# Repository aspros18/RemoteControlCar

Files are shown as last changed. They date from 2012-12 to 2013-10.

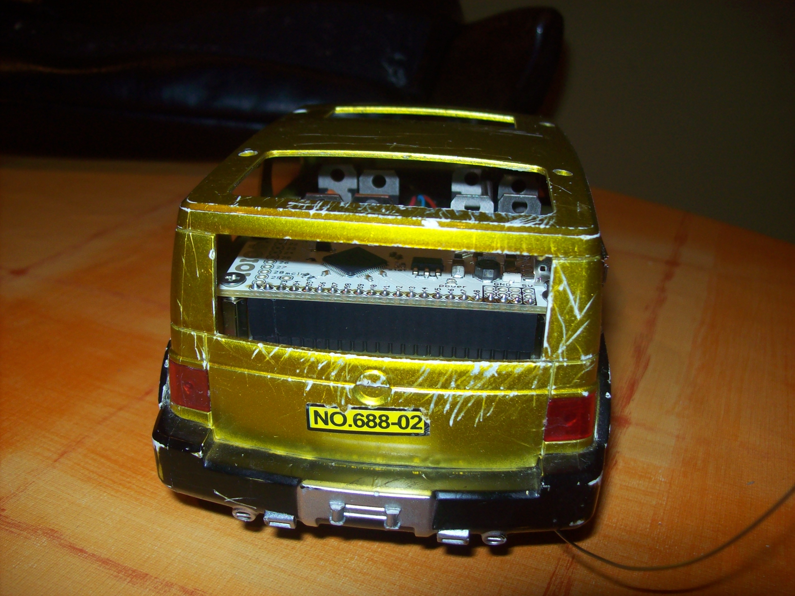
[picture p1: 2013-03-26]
photos/testmodel_bottom.JPG

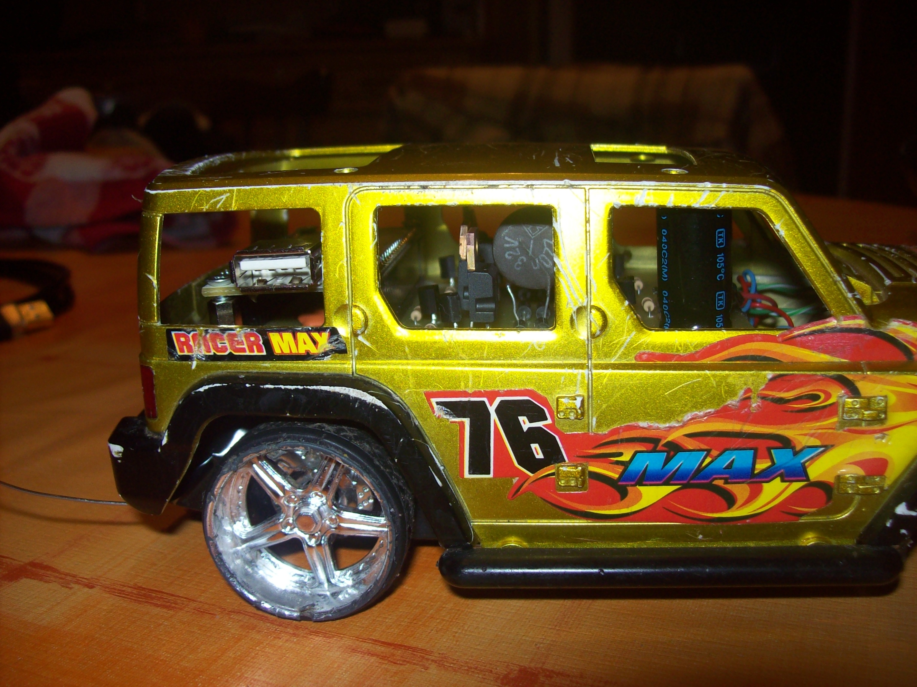
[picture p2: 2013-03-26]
photos/testmodel_side.JPG

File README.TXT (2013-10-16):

Git URL: https://github.com/fzoli/RemoteControlCar

Beszerzés
---------

Hordozható kiadás:
https://github.com/fzoli/RemoteControlCar/raw/master/bin/rel-portable.zip

Windows telepítő:
https://github.com/fzoli/RemoteControlCar/raw/master/Setup.msi

Linux telepítő:
https://github.com/fzoli/RemoteControlCar/raw/master/linux-installer.bsx

OS X telepítő:
https://github.com/fzoli/RemoteControlCar/raw/master/mac-installer.dmg

Android alkalmazás:
https://github.com/fzoli/RemoteControlCar/raw/master/android/RemoteControlCar/bin/RemoteControlCar.apk

A projektet bemutató videófelvételek a videos könyvtárban találhatók meg.
A járműről fényképek a photos könyvtárban, képernyőképek a snapshots
könyvtárban. A szakdolgozat digitális változata: thesis.pdf

Bevezetés
---------

A projekt célja egy távirányítós autó vezérlése interneten át.

Az autó vezérlése Android operációs rendszerrel futó mobiltelefon segítségével valósul meg.

A telefon felhasznált eszközkészlete:
- hátsó kamera, ami segítségével lehet látni, mi van az autó előtt
- giroszkóp, ami segítségével meg lehet tudni a gyorsulás és kanyarodás mértékét valamint az út lejtését (ha nincs fék az autón, az emelkedő/lejtő adat alapján megoldható, hogy egy helyben álljon az autó bármikor, ha azt akarjuk)
- GPS vevőt, ami segítségével megbecsülhető a pillanatnyi sebesség és megtudható a kellően pontos tartózkodási hely
- USB port, ami segítségével - egy SparkFun által gyártott mikrovezérlő - az IOIO for Android (DEV-10748) köthető össze a telefonnal. A mikrovezérlőhöz tartozik egy Java nyelvre írt API, ami segítségével ADB (Android Debug Bridge) vagy ADK (Accessory Development Kit) kapcsolaton keresztül a telefon képes kommunikálni a külvilággal. Az API automatikusan kapcsolódik az eszközhöz, nem fontos, melyik kapcsolaton keresztül, de az ADB van előnyben részesítve.
- mobilhálózat, ami segítségével HSPA vagy 3G mobilinternetet használva elküldhető a videó jel, a statisztika és foghatóak a vezérlő jelek
- mobilakku, ami ellátja a mobiltelefont árammal. Azt is jó látni interneten keresztül, hány %-on áll az aksi.

A mikrovezérlő célja:
- vezérelni az autót a telefonnal
- az autó akkumulátorának töltöttségi szintjének megszerzése

Egyéb eszközök:
- kézzel állítható, kétállású kapcsoló, ami eldönti, hogy a beépített mikrovezérlő (ami a gyári távirányító jelének segítségével vezérli az autót) vagy a telefon mikrovezérlője (ami az internetről kapott utasításokkal vezérli az autót) legyen aktív. Erre azért van szükség, hogy ne történhessen meg az, hogy mindkét mikrovezérlő egyazon időben jelzést adjon le és túlfeszültséget okozzon az autó áramkörében
- a lista még bővülni fog olyan dolgokkal mint pl. ellenállás

A hálózati kommunikáció terve:
------------------------------

A kommunikáció SSL titkosítást használva socketek segítségével történik.
A tanúsítványokban szereplő CN (Common Name) mező alapján történik a felhasználó számítógépek és emberek azonosítása, tehát nincsenek felhasználónevek és jelszavak.
Az összes tanúsítvány egyetlen kiállítótól (CA) származik és mind a socket szerver, mind a socket kliensek csakis ebben az egy kiállítóban bízik meg.
Ez azt eredményezi, hogy az összes olyan tanúsítványt elfogadják, amiket a konkrét CA állított ki, de az összes többit elutasítják.

Az SSL többféle próbának is aláveti a socketeket mielőtt létrejönne a kapcsolat:
- megnézi, hogy megbízható-e a tanúsítvány (vagyis inkább a CA)
- megnézi, hogy nem járt-e le a tanúsítvány
- ellenőrzi a hostnevet

A hostnév-ellenőrzés ki van kapcsolva, mert a szabvány szerint a szerver hostnevének és a tanúsítványában szereplő CA mezőnek meg kell egyeznie.
Fentebb írtam, hogy a CA mezőt én a felhasználók azonosítására használom (amolyan felhasználónév szerűség), másrészt a szervernek nem feltétlenül van hostneve vagy a hostnév változó (Pl. IP cím alapján is lehet szerverhez kapcsolódni).

Az egyszerűsített kapcsolati ábra:
Host <-> Bridge <*> Controller

Jelmagyarázat:
<-> egy-egy kapcsolat
<*> egy-sok kapcsolat
Host: a mobiltelefon által indított kliens socket (magyarban is host)
Bridge: egy olyan socket szerver, ami kliens socketek kapcsolódására vár (magyarra fordítva: híd)
Controller: azok a kliens programok, amik segítségével vezérelhető az autó (magyarra fordítva: vezérlő)

Host:
-----

Socket oldalról megközelítve:
A host az én esetemben egy mobiltelefon, ami legtöbbször mobilinternetet - ritkábban Wi-Fi hálózatot és akkor belső IP alapján is lehet címezni - használ  arra, hogy fel tudja venni a kapcsolatot a híddal. Socket szempontjából ő kliens szerepet tölt be. Ennek az az oka, hogy az összes internetes IPv4 cím ki lett már osztva és az internetszolgáltatók minden trükköt bevetnek, hogy ki tudják szolgálni az összes internetet használni akaró gépet. A mobilszolgáltatók ezért NAT-olt IP címet osztanak ki a mobilinternetet használó gépeknek. Ezzel a trükkel egy internetes IP cím (rövidebben WAN IP) több géphez is tartozhat, tehát több gépet ki lehet szolgálni, de van egy hátránya is - amiről a mobilinternetezők nagy része nem is tud - mégpedig az, hogy nincs egy elérhető aktív port sem. Mivel nincs aktív port, hiába üzemeltetünk szervert a telefonon, azt az internetről nem lehet elérni, vagyis csak kliens szerep lehetséges.

A kamera elérése:
A telefon kamerájának képkockái MJPEG streameléssel jutnak el a hídhoz.
Eredeti elképzelésem szerint saját magam olvastam volna a kamera képét és küldtem volna a socket servernek.
A probléma ott kezdődött, hogy az android API nem éppen programozóbarát ha médiáról van szó.
Egyrészt csak akkor hajlandó képkockákat adni, ha azt felületen is megjelenítem (és ennek nem sok értelme van) valamint az eseménykezelőben egy bájt tömböt kapok, amiben YUV formátumú kép van. Ezzel még nem is lenne gond, mert ha valakinek csak a fekete-fehér tartomány kell, akkor még örül is neki, de ha színes képet szeretne az én telefonom kb. 800 ezredmásodpercig dolgozik rajta és akkor még nem is méreteztem át, nem is tömörítettem JPEG formátumba. Olyan 0.7 FPS érhető el így összességében. Gondoltam utánanézek már kész androidos programoknak, amik tudnak videót streamelni. A sok androidos program közül egy megfelelően működőt találtam is, aminek a neve IP Webcam. Java csomag alapján keresve "com.pas.webcam". Ez volt az egyetlen olyan program, ami már megfelelő FPS-t tudott és nem észleltem késést sem. Meg is néztem az okát (hogy hogyan, az már más kérdés). Natív kódot használtak fel, amit C nyelven írtak meg. (Az Android is támogatja a natív kódokat. Bővebben: NDK - Native Development Kit)
Az IP Webcam program HTTP szervert használ és lehetőség van felhasználónév és jelszó beállítására, valamint megadhatjuk a szerver portját, a JPEG képek paramétereit (felbontás, FPS, képminőség) és hogy induljon-e el a telefon indulásakor a program, hogy bármikor hozzá lehessen férni a kamerához.

A telefonon futó program terve:
A telefonon egy Android service fog futni, amit egy egyszerű Activity felületről lehet majd elindítani ill. leállítani.
A service ha leállítódik valami ok miatt (pl. kevés a memória), úgy lesz beállítva, hogy amint lehetséges, induljon el.
Ha a telefon újraindulna miközben a service fut (pl. SD kártyáról fut vagy 100 program és szegény kártya nem bírja olyan gyorsan adni az adatokat mint kéne), a service az OS (operációs rendszer rövidítése) felállása után szintén elindul.
A service az elindulása után azonnal kapcsolódni próbál a hídhoz, ha nem sikerül percenként próbálkozik.
Ha a kapcsolat megszakad, azonnal elindul a kapcsolódás folyamata.
Ezzel minden nem várt hibára megtörtént az óvintézkedés.
A service elindulásakor, ha nem fut az IP Webcam program, akkor az API-ja segítségével a service elindítja azt. (Az ip-webcam könyvtárban további infó.)
A service elindítása előtt a felületen a menüből kezdeményezhető további beállítás.
Itt kell megadni:
- a híd címét (host vagy IP) és portját (amin a socket servlet figyel)
- a tanúsítvány publikus kulcsát (crt fájl) és privát kulcsát (key fájl), amivel a hídhoz kapcsolódik és titkosít.
- a tanúsítvány kiállítójának publikus kulcsát
- mennyi időközönként küldjön statisztikát a telefon
Opcionális beállításként megadható a híd tanúsítványának CN mezője, csak a biztonság kedvéért.
Előfordulhat, hogy rossz címet állítottunk be és nem a híd van címezve. Ez esetben ha a CN mező meg van adva, kiküszöbölhető a fölösleges kapcsolódás és azonnal egyértelmű hibajelzést kapunk. Ha nincs megadva a CN mező, a program percenként fölöslegesen fog próbálkozni, konkrét hibát nem jelezve.

A hang stream, eredetileg kikapcsolt és kérhető lesz bekapcsolásra. Kikapcsolása esetén elég a socket streamet lezárni és kezelni kell a kivételt.
A streamet az android beépített szolgáltatása (MediaRecorder.AudioEncoder.AAC) fogja szolgáltatni és a híd fogja tovább adni a vezérlőknek.

Bridge:
-------

A hídnak két szerepköre van:
- vár a hostra - amitől a videót és a statisztikát kapja és akinek a vezérlőjelet küldi majd
- kiszolgálja a vezérlőket - amik irányítani szeretnék az autót - és eldönti, hogy ki vezérelheti az autót, ha több kérés van egy időben

Úgy terveztem meg a socket alapú kommunikációkat, hogy a híd el tudja dönteni, mi célja lesz a kapcsolatnak és egy időben több kapcsolatot kezelhessen.
A híd esetén a host CN mezőjét kötelező megadni, mert a híd ez alapján tudja, hogy a socket kliens vezérlő-e vagy host. EZ NAGYON FONTOS!!!
A híd esetében megadható több CN mező is, amik segítségével lehet tudni, mely tanúsítványok lesznek a hostok ha esetleg több autó is távvezérelt lesz a jövőben. (Meg lehetett volna oldani úgy is, hogy a socket kliensek még a kapcsolatazonosító kérése előtt közölték volna, hogy ők hostok vagy vezérlők, de ez esetben a híd nem tudna pontos listát adni a hostokról.)

[Opcionális terv: A híd mellé lehetne egy webszervert is tenni. Regisztrálhatnának internetről mások, akiknek el lett adva egy ilyen autó és van hozzá mobiltelefonjuk. A webszerver is SSL-t használna az alapértelmezett 443-as porttal. Itt akár tanúsítványt is generáltathatnának (hostjukhoz és vezérlőjeikhez) így a híd socket servere megbízhatónak találná őket és szintén tudná ki a host és ki a vezérlő. A híd szolgáltatása havidíjas is lehetne és azoknak lenne jó, akik nem szeretnének saját híd szervert üzemeltetni. A host mikrovezérlő kódját ez esetben úgy kellene megtervezni, hogy interface alapú legyen és a felületről több autó típust lehessen választani az implementált osztályok alapján. Szép álom lenne, ha a mobilinternetes szolgáltatókkal meg lehetne egyezni, hogy ne mérjék a forgalmat és kapnak a bevételből :-) ]

Host felőli kapcsolatok:
1. MJPEG stream: hídnak letöltés, hostnak feltöltés
2. Statisztika adatok: objektumos stream, hídnak letöltés, hostnak feltöltés
3. Vezérlő parancsok a hídtól (az autónak és a telefonon futó programnak): objektumos stream, hídnak feltöltés, hostnak letöltés

Vezérlő felőli kapcsolatok:
1. MJPEG stream: hídnak feltöltés, vezérlőnek letöltés
2. Statisztika adatok (a hostról és a hídról): objektumos stream, hídnak feltöltés, vezérlőnek letöltés
3. Vezérlő parancsok a vezérlőtől (a hostnak és a hídnak): objektumos stream, hídnak letöltés, vezérlőnek feltöltés

Bővebb magyarázat:
- A kapcsolatok előtt a számozás kapcsolatazonosítót és prioritási sorrendet is jelent.
- A híd a hostnak főként autóvezérlő utasításokat közöl (a 3-mas kapcsolaton át), de a telefonnak közölheti azt is,
  hogy hagyja abba az MJPEG streamelést vagy éppen kezdje el.
- A vezérlő a hídnak főként autóvezérlő utasításokat ad, de üzenhet a hídnak is, hogy szeretné átvenni az autó irányítását.
- A híd is üzenhet a vezérlőnek, ha éppen elvették tőle az irányítást, jelezze a felületen.

A kapcsolat kialakítása a következő módon valósul meg:
A kliens három kapcsolatot alakít ki ugyan azzal a sockettel, a kapcsolat létrejötte után új szálban kezdődik meg a feldolgozás.
A szerver amíg aktívan fut (tehát a Socket server nincs bezárva) cikluson belül mindig várja a klienseket és ha létrejön egy SSLSocket, ő is külön szálban dolgozik vele tovább, hogy képes legyen több kapcsolatot kiszolgálni egy időben.

A kapcsolat kialakításának lépései: (Szerver alatt a híd socket szerverét értem.)
0. A kliens socket kapcsolódik a szerver sockethez és sikerül az SSL kézfogás, létrejön a kapcsolat és mindkét oldalon egy SSLSocket objektum.
1. a) A szerver a kliens-tanúsítvány CN mezejének alapján megtudja, hogy a kliens host vagy vezérlő és hogy pontosan kivel is van dolga.
   b) A szerver megnézi, hogy az adott szerepkörben az adott névhez hány kapcsolat van már kialakítva.
   c) A szerver inkrementálja a B pontban kapott számot és így megkapja az aktuális kapcsolat azonosítóját
      és a fenti felsorolás alapján már tudja is, mire lesz használva a kapcsolat.
2. A szerver elküldi a kliensnek a kapcsolatazonosítót. Másképp fogalmazva: A kliens lekéri a kapcsolatazonosítót.
3. Mindkét oldal a kapcsolatazonosító alapján együttműködve kezeli a kapcsolatot.
4. Bármelyik oldal lezárhatja a kapcsolatot, ha úgy dönt. Ekkor befejeződik a kommunikáció.

Ha a hídra ugyan azzal a tanúsítvánnyal kapcsolódnak több helyről, a híd a régebbi kapcsolatokat bezárja.
Így ki van kerülve az, hogy két helyről vezérelhessék az autót ellentmondásos üzenetet leadva mint pl. menj jobbra és balra is.

Jogkezelés:
Előfordulhat olyan eset, hogy egy autót több vezérlő is szeretne irányítani.
Erre azt találtam ki, hogy csinálok a hídra egy tanúsítvány-prioritás listát.
A nagyobb prioritású vezérlő bármikor elveheti a vezérlést a kisebb prioritású vezérlőktől, de egyébként minden vezérlő kapcsolódhat a hídhoz és minden
információt láthat, csak a vezérléstől vannak megfosztva.
Amint felszabadul a vezérlés, bárki kérheti az autó vezérlését prioritástól függetlenül és meg is kapja.
(Kérni lehet akkor is, ha éppen vezérlik az autót, de az csak kérvényt jelent, semmi többet. Amint felszabadul a vezérlés az első kérvényt benyújtó meg is kapja.)
(Ha a prioritáslistában egyetlen név szerepel, akkor úgy fog funkcionálni, mint ha root lenne, mivel mindenki felett áll ez esetben.)
Ha nagyobb prioritású kapcsolódik a hídhoz, mint aki vezérli az autót, addig amíg nem kéri a vezérlést, nem veszi el a híd az aktuális vezérlőtől az irányítást.
Aki nem szerepel a prioritáslistában, az olyan, mint ha a legutolsó utolsó helyen szerepelne a listában és a többi - listában nem szereplő - felhasználóval egyenrangúnak számít, tehát ők egymástól nem tudják elvenni a vezérlést.
Ha a vezérlő sokáig nem cselekszik, tehát nincs a gép előtt, a vezérlést elveszi a híd tőle.

Internet sávszélesség:
A híd létrejöttének fő célja az volt, hogy egyetlen egy kapcsolat (ami valójában három socket kapcsolat) legyen a mobilinternet oldaláról és az is takarékos legyen mivel forgalom- és sebességkorlátos az internet.
A hídba be van téve egy olyan sávszélesség csökkentő funkció is, hogy csak akkor kéri az MJPEG streamet a hosttól, ha van legalább egy vezérlő kapcsolódva hozzá.

Konfig fájl:
A híd esetén is meg kell adni a tanúsítvány publikus és titkos kulcsának az elérhetőségét és a kiállító publikus kulcsának az elérhetőségét.
A tanúsítvány prioritásokat és a hostlistát is itt kell megadni, de ha bevezetésre kerül egy webes felület, átkerülnek egy közös adatbázisba.

Controller:
-----------

A vezérlő az a program, ami megjeleníti az autó adatait és ha van lehetősége vezérli az autót.
Ez egy PC-n futó java alapú desktop alkalmazás lényegében, ami szintén a hídhoz kapcsolódik socket kliensként.
A felületen lehetőség van - és kötelező is első induláskor - beállítani a híd címét és portját valamint a tanúsítvány publikus és titkos kulcsát és a kiállító publikus kulcsát.
A kiállító kulcsára azért van szükség mert kliens oldalon is ellenőrizve van a szerver tanúsítvány megbízhatósága, nem csak szerver oldalon, hogy a man-in-middle támadás lehetetlen legyen.
A vezérlés billentyűzet és egér segítségével történik.
Az egérrel pontos utasítást lehet adni mind sebesség, mind irány terén.
A billentyűzettel egyszerűbb, de durvább irányítást érhet el a felhasználó és több vezérlés mód közül választhat.
(A vezérlési módok a durvaságot szabályozzák pl. előre nyílra egyenletesen gyorsuljon fel vagy földkaparással max grafttal induljon el)

Egy kis trükk:
--------------

Egyes mobilszolgáltatók csomagjaiban a webböngészés nem számít bele a forgalomkorlátba.

Ez esetben socketek helyett mondjuk Tomcat webszervert lehetne használni.
- A terv lényege ugyan az, csak a kapcsolatazonosítók helyett HTTP címzés lenne használva.
- Az MJPEG stream HTTP POST-tal streamelhető a hídnak - ami a Tomcat webszerver.
- A vezérlő utasítások JSON-nal objektummá alakíthatók Stringből és objektumból Stringre, és a HTTP tartalom is gond nélkül használható streamelés céljára.

UPDATE: Utólag kiderült, hogy csak a letöltés nem számít bele, és mivel a telefonon a kliens 99%-ban feltöltést bonyolít le, elvetett ötlet.

Továbbfejlesztés
----------------

További két socket kapcsolat segítségével megoldható lenne, hogy a telefon mikrofonjából megkapjuk a hangot is a kép mellé és a vezérlő számítógép mikrofonjából meg a telefonon játsszunk le hangot.
A telefonból érkező hang stream ki/be kapcsolható lenne, alapértelmezetten ki lenne kapcsolva takarékosság miatt.
Az autót vezérlő kliens tudná csak ki/be kapcsolni a streamet és csakis ő tudna hang streamet küldeni a telefonnak.
A sávszélesség kímélése érdekében a Javara írt Tritonus API-t használva lehetne tömöríteni GSM vagy MP3 formátumba a monó 16 bites PCM-ről. (Mondjuk GSMFormatConversionProvider segítségével.)
Egyéb pluginok: http://www.tritonus.org/plugins.html
Példa: http://www.jsresources.org/examples/GSMEncoder.java.html
Ha a Tritonus még sem használható út, marad a GZipInputStream és társa a GZipOutputStream.
Vagy egy másik út: http://www.jsresources.org/apps/9159_TimeTurner.pdf

Az autón lévő tartó, amiben a mobil lesz, lehetne motor által vezérelhető, hogy a kereszteződéseket be lehessen látni és igény szerint hátra is lehessen tekinteni.
A giroszkóp adatait a telefon programja csak az alapállásban adná le a megbízhatóság miatt. (Vagy ha szükség van rá, akkor csak a motor mozgása közben lenne inaktív és az algoritmus meg lenne írva úgy, hogy több helyzetből is jó adatokat közöljön.)

A telefont tartó eszköz lehetőleg védje a telefont a külső támadások ellen és az eső ellen, kulccsal zárható legyen.
Ha ez meg lett oldva, a kábeleket is jó lenne biztonságosan elvezetni szintén védve és a kapcsolót, ami átkapcsolhat internetes vezérlésről, azt is a kulccsal
zárt, védett helyen belülre kéne elhelyezni.

Egy harmadik kliens alkalmazásként lehetne írni egy admin felületet, amivel a belépett felhasználókat lehet menedzselni (priorítás, ban, kick).
Lehetne egy SSL alapú weboldal is, ahonnan regisztráció után letölthető lenne a kliensekhez használható tanúsítvány.

Repülőmodel átalakítása, vezérlés kibővítése a 3. dimenzióval (fel/le emelkedés).
Időjárásadatok begyűjtésére is használható lenne.

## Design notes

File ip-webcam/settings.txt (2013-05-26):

320x240		resolution
1024x768	photo resolution
32		quality
Landscape	orientation
No limit	FPS limit
Default		focus mode

IPv4		primary address family
8080		port

Enabled		audio mode
false		disable notification
true		prevent going to sleep
false		stream on device boot

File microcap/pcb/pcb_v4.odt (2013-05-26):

Made in Hungary by Zoltán Farkas.

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
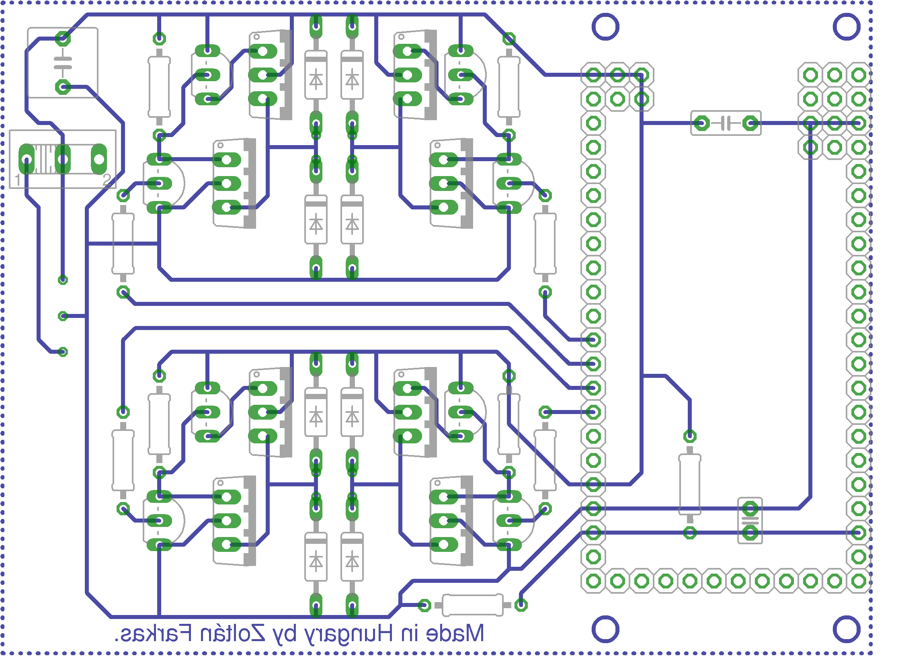
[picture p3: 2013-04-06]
microcap/pcb/design_v4.png

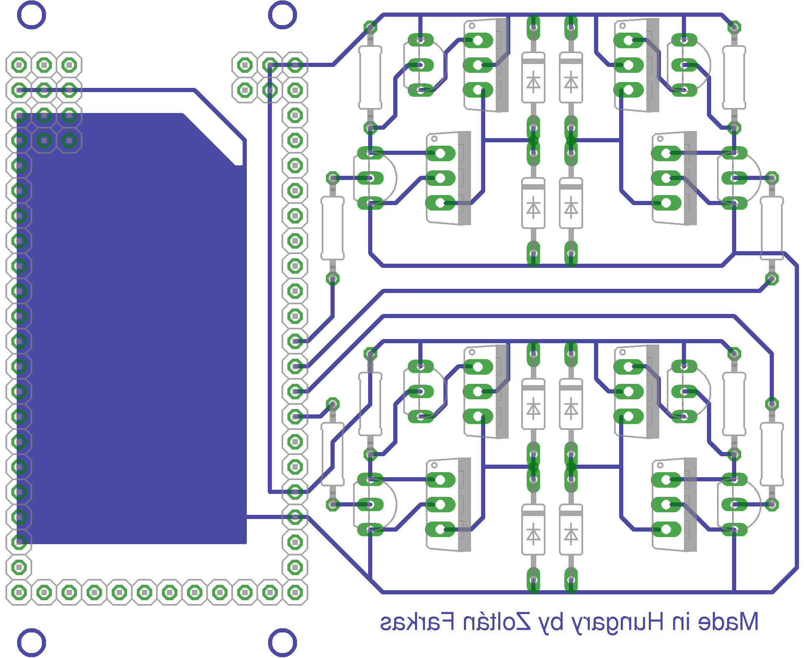
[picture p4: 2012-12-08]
microcap/pcb/design_v2.png

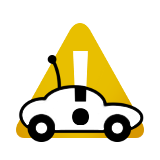
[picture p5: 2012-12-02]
android/RemoteControlCar/design/ic_warning.png

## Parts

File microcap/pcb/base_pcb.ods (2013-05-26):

 |  |  |  | Q5 |  | D2
 | R2 | Q1 |  |  | D1 |  | Q6 | Q4 | R3 |  | R3' | Q4' | Q6'
 |  |  |  |  | M
 | Q2 |  |  |  |  |  |  |  | Q3 | B2 | Q3'
R1 |  |  | Q7 |  | D3 | D4 | Q8 |  |  | B1 |  | Q8'
 |  |  |  |  |  |  |  |  |  | A1
 |  |  |  |  |  |  |  |  |  | A2

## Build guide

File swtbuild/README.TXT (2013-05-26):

README:

http://mchr3k.github.com/swtjar/

TODO:
- Az elkészült jar fájlból hiányoznak:
  a) a képfájlok (controller és bridge resource csomagokból)
  b) a log4j properties fájl
  c) az összes nyelvi fájl (properties fájlok)
- A Splash Screen nem állítódik be a manifest fájlba.

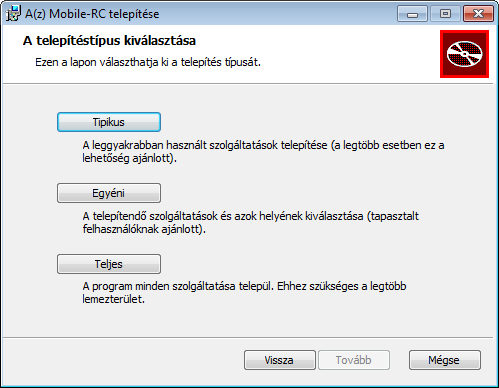
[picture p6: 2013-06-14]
snapshots/desktop/win_setup/2.png

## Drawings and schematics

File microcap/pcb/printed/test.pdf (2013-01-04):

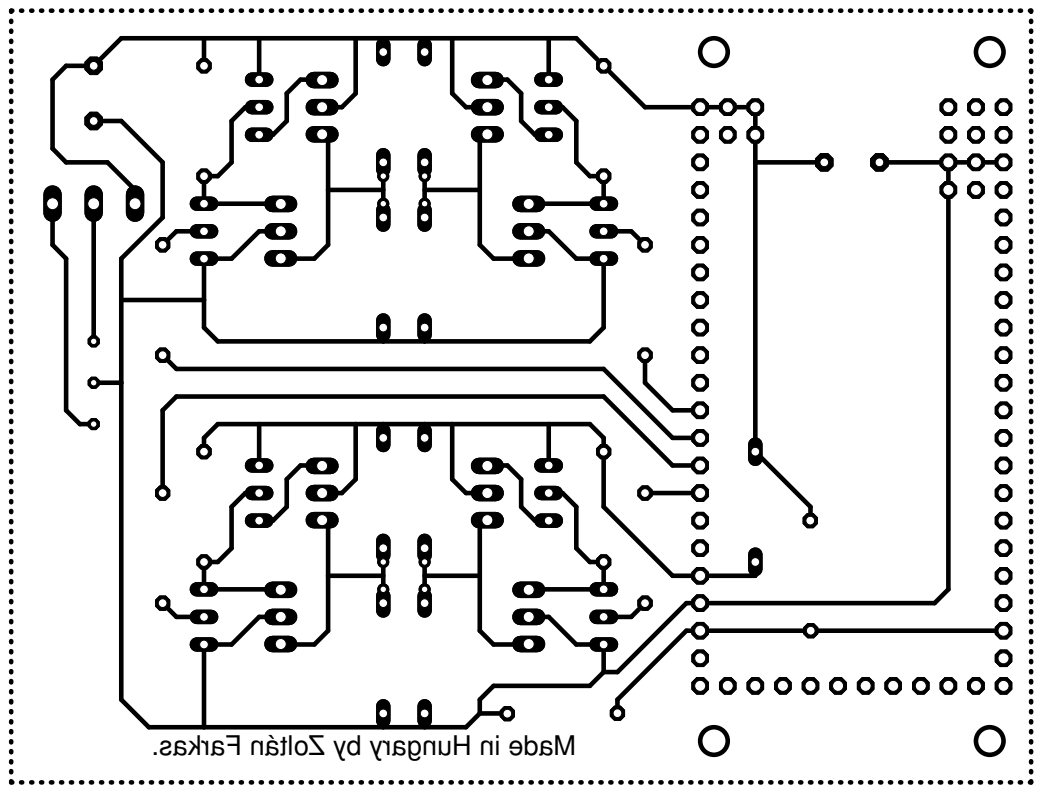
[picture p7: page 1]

. sakr aF nátl oZ yb yr agnu Hni eda M

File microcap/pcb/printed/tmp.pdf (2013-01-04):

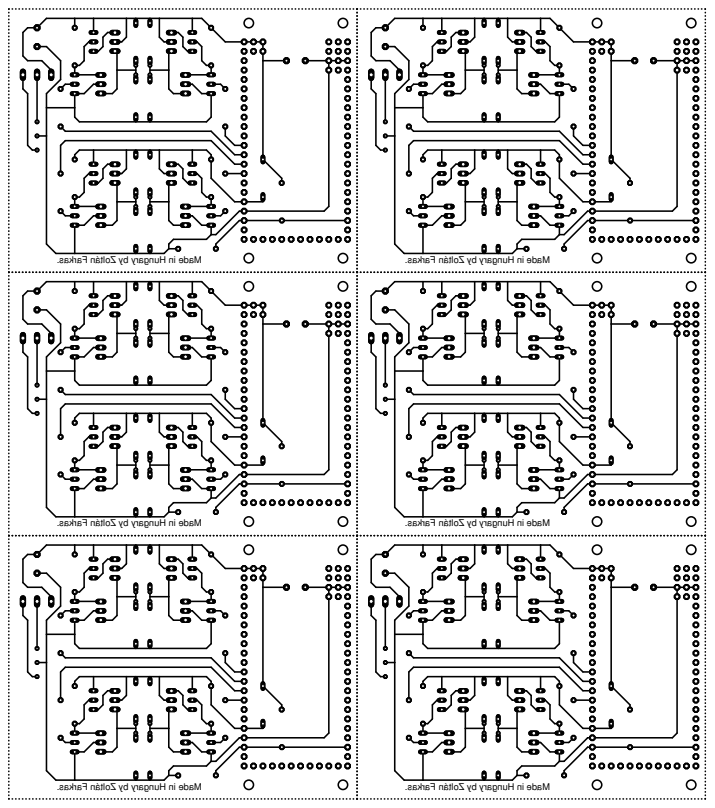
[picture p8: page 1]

. sakr aF nátl oZ yb yr agnu Hni eda M

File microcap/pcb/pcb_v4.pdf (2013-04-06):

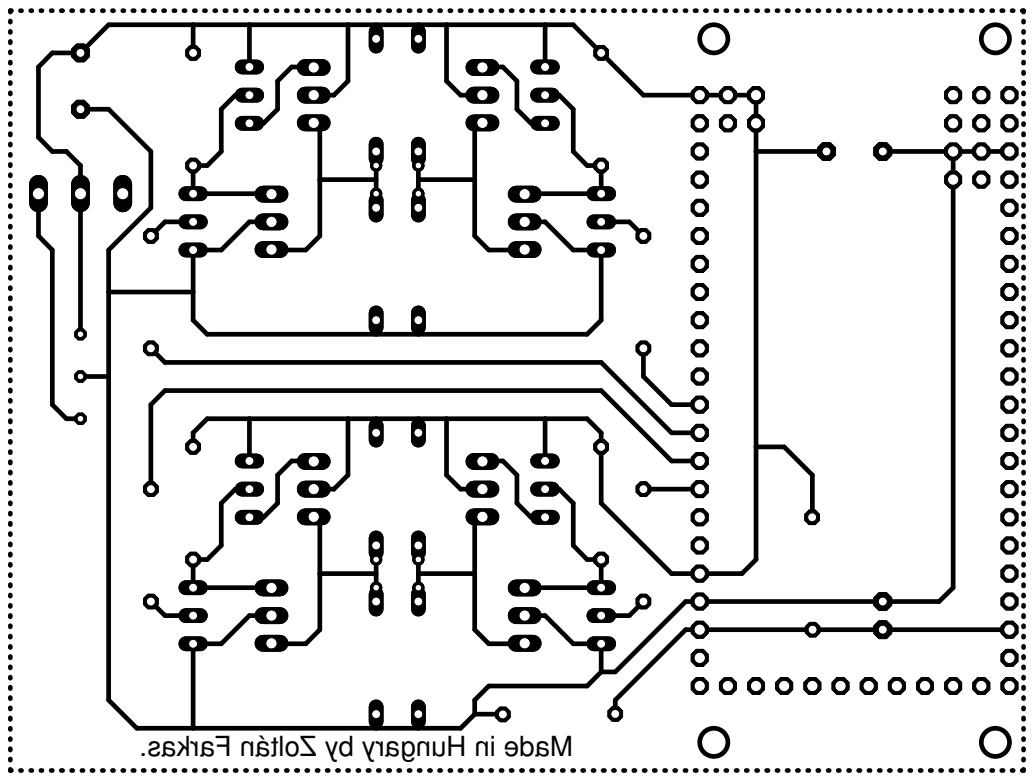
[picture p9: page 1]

. sakr aF nátl oZ yb yr agnu Hni eda M

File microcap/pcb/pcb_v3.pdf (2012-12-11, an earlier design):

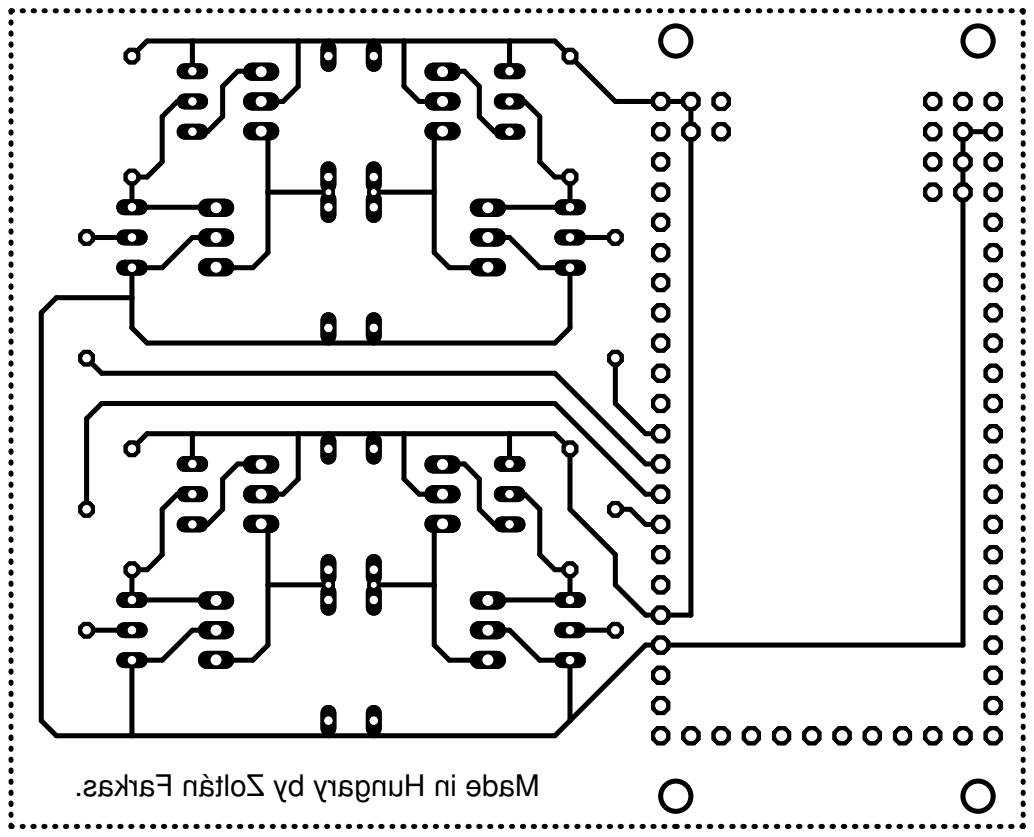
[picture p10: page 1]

. sakr aF nátl oZ yb yr agnu Hni eda M

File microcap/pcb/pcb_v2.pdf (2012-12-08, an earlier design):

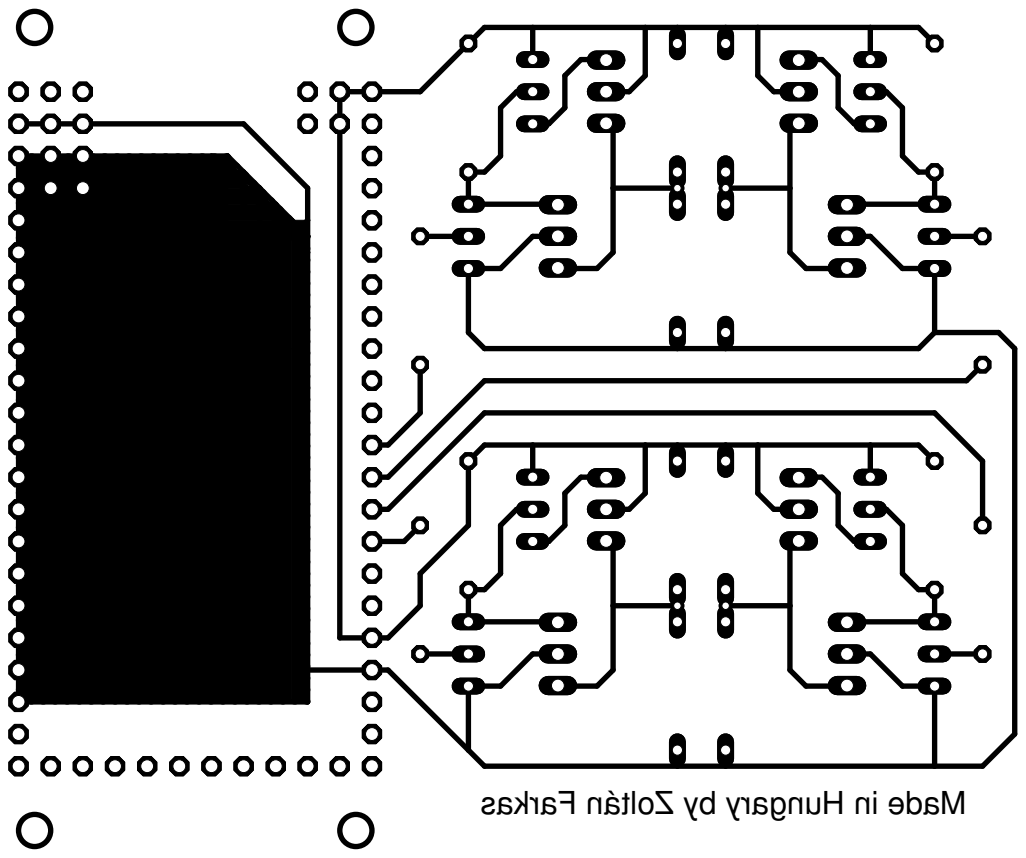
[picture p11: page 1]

sakr aF nátl oZ yb yr agnu Hni eda M

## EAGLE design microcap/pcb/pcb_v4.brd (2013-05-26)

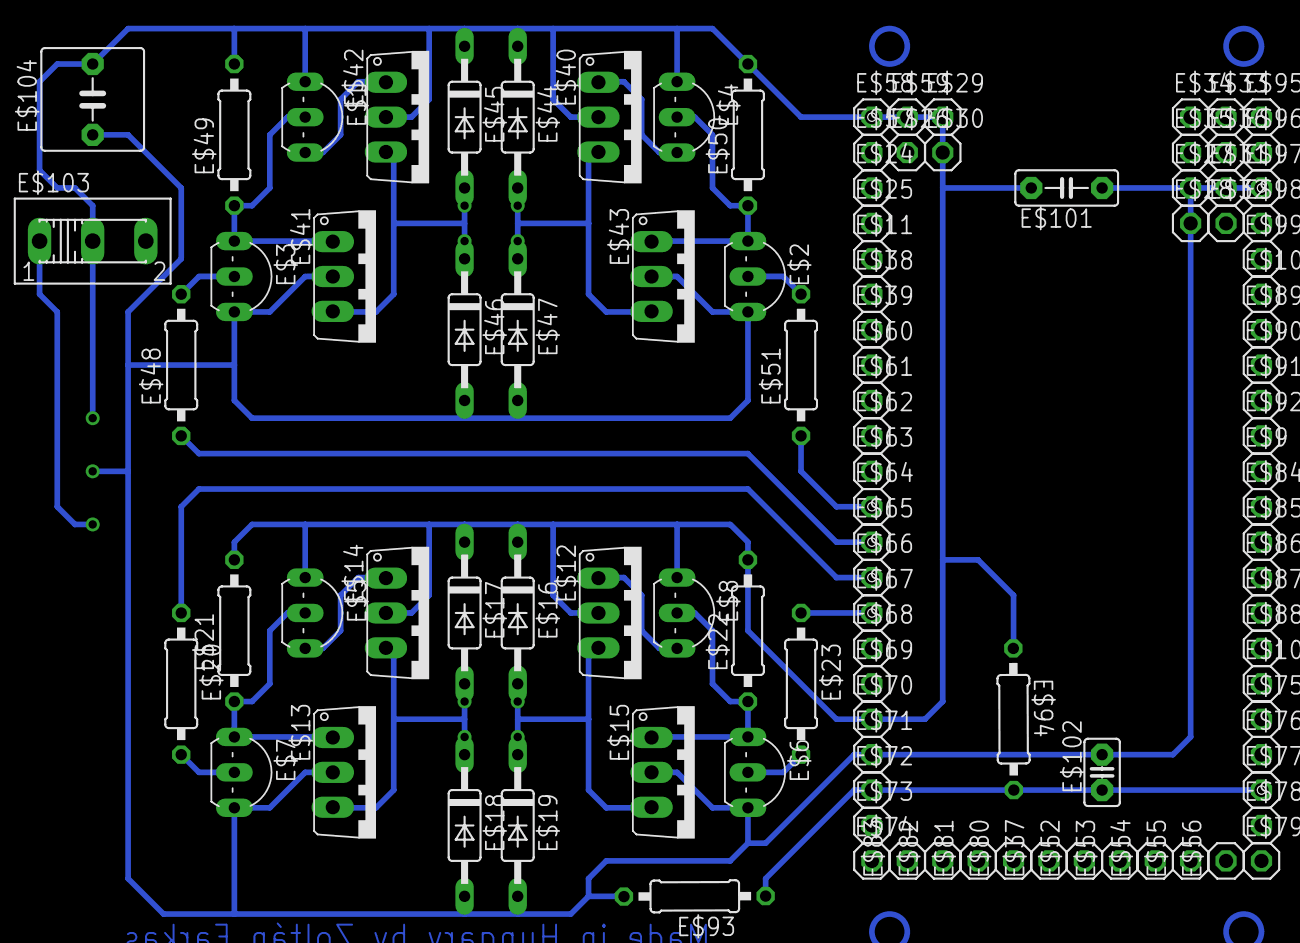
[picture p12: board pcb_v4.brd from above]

Board: 2 copper layers, 104 parts (0 on the bottom side), 18 nets.

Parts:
E$1, E$2, E$3, E$4, E$5, E$6, E$7, E$8: TO92-CBE
E$9, E$10, E$11, E$24, E$25, E$26, E$27, E$28, E$29, E$30, E$31, E$32, E$33, E$34, E$35, E$36, E$37, E$38, E$39, E$52, E$53, E$54, E$55, E$56, E$57, E$58, E$59, E$60, E$61, E$62, E$63, E$64, E$65, E$66, E$67, E$68, E$69, E$70, E$71, E$72, E$73, E$74, E$75, E$76, E$77, E$78, E$79, E$80, E$81, E$82, E$83, E$84, E$85, E$86, E$87, E$88, E$89, E$90, E$91, E$92, E$95, E$96, E$97, E$98, E$99, E$100: 1X01
E$12, E$13, E$14, E$15, E$40, E$41, E$42, E$43: T-30_V
E$16, E$17, E$18, E$19, E$44, E$45, E$46, E$47: C2992
E$20, E$21, E$22, E$23, E$48, E$49, E$50, E$51, E$93, E$94: 0207/10
E$101: C5B2.5
E$102: C2.5-2
E$103: 255SB
E$104: C5B7.2

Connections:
S$2: E$2.C, E$4.B, E$50.1
S$5: E$3.B, E$48.2
S$6: E$2.B, E$51.2
S$7: E$5.B, E$7.C, E$21.1
S$8: E$45.A, E$46.C
S$9: E$1.B, E$3.C, E$49.1
S$12: E$17.A, E$18.C
S$15: E$23.1, E$67.1
S$16: E$6.C, E$8.B, E$22.1
S$17: E$6.B, E$23.2
S$18: E$51.1, E$64.1
S$19: E$16.A, E$19.C
S$21: E$7.B, E$20.2
S$22: E$44.A, E$47.C
S$23: E$48.1, E$65.1
S$28: E$1.C, E$4.C, E$5.C, E$8.C, E$16.C, E$17.C, E$21.2, E$22.2, E$29.1, E$44.C, E$45.C, E$49.2, E$50.2, E$58.1, E$59.1, E$70.1, E$101.2, E$103.2, E$104.2
S$29: E$2.E, E$3.E, E$6.E, E$7.E, E$18.A, E$19.A, E$46.A, E$47.A, E$71.1, E$97.1, E$101.1, E$104.1
S$36: E$20.1, E$66.1

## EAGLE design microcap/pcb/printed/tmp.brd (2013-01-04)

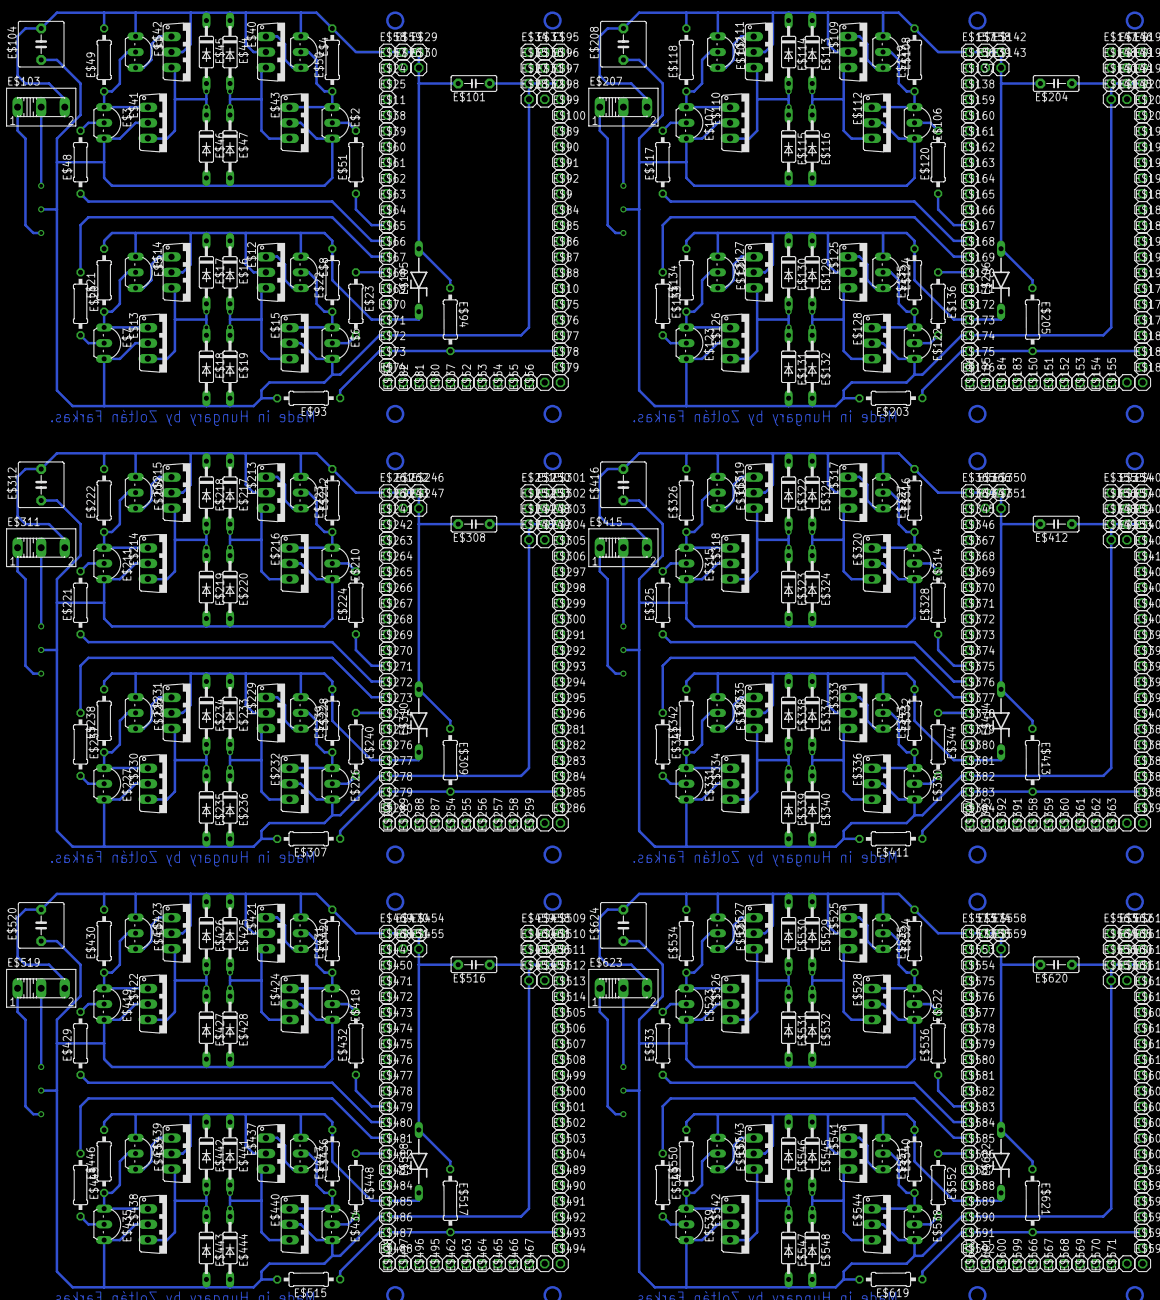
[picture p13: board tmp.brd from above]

Board: 2 copper layers, 624 parts (0 on the bottom side), 114 nets.

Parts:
E$1, E$2, E$3, E$4, E$5, E$6, E$7, E$8, E$102, E$106, E$107, E$108, E$121, E$122, E$123, E$124, E$209, E$210, E$211, E$212, E$225, E$226, E$227, E$228, E$313, E$314, E$315, E$316, E$329, E$330, E$331, E$332, E$417, E$418, E$419, E$420, E$433, E$434, E$435, E$436, E$521, E$522, E$523, E$524, E$537, E$538, E$539, E$540: TO92-CBE
E$9, E$10, E$11, E$24, E$25, E$26, E$27, E$28, E$29, E$30, E$31, E$32, E$33, E$34, E$35, E$36, E$37, E$38, E$39, E$52, E$53, E$54, E$55, E$56, E$57, E$58, E$59, E$60, E$61, E$62, E$63, E$64, E$65, E$66, E$67, E$68, E$69, E$70, E$71, E$72, E$73, E$74, E$75, E$76, E$77, E$78, E$79, E$80, E$81, E$82, E$83, E$84, E$85, E$86, E$87, E$88, E$89, E$90, E$91, E$92, E$95, E$96, E$97, E$98, E$99, E$100, E$137, E$138, E$139, E$140, E$141, E$142, E$143, E$144, E$145, E$146, E$147, E$148, E$149, E$150, E$151, E$152, E$153, E$154, E$155, E$156, E$157, E$158, E$159, E$160, E$161, E$162, E$163, E$164, E$165, E$166, E$167, E$168, E$169, E$170, E$171, E$172, E$173, E$174, E$175, E$176, E$177, E$178, E$179, E$180, E$181, E$182, E$183, E$184, E$185, E$186, E$187, E$188, E$189, E$190, E$191, E$192, E$193, E$194, E$195, E$196, E$197, E$198, E$199, E$200, E$201, E$202, E$241, E$242, E$243, E$244, E$245, E$246, E$247, E$248, E$249, E$250, E$251, E$252, E$253, E$254, E$255, E$256, E$257, E$258, E$259, E$260, E$261, E$262, E$263, E$264, E$265, E$266, E$267, E$268, E$269, E$270, E$271, E$272, E$273, E$274, E$275, E$276, E$277, E$278, E$279, E$280, E$281, E$282, E$283, E$284, E$285, E$286, E$287, E$288, E$289, E$290, E$291, E$292, E$293, E$294, E$295, E$296, E$297, E$298, E$299, E$300, E$301, E$302, E$303, E$304, E$305, E$306, E$345, E$346, E$347, E$348, E$349, E$350, E$351, E$352, E$353, E$354, E$355, E$356, E$357, E$358, E$359, E$360, E$361, E$362, E$363, E$364, E$365, E$366, E$367, E$368, E$369, E$370, E$371, E$372, E$373, E$374, E$375, E$376, E$377, E$378, E$379, E$380, E$381, E$382, E$383, E$384, E$385, E$386, E$387, E$388, E$389, E$390, E$391, E$392, E$393, E$394, E$395, E$396, E$397, E$398, E$399, E$400, E$401, E$402, E$403, E$404, E$405, E$406, E$407, E$408, E$409, E$410, E$449, E$450, E$451, E$452, E$453, E$454, E$455, E$456, E$457, E$458, E$459, E$460, E$461, E$462, E$463, E$464, E$465, E$466, E$467, E$468, E$469, E$470, E$471, E$472, E$473, E$474, E$475, E$476, E$477, E$478, E$479, E$480, E$481, E$482, E$483, E$484, E$485, E$486, E$487, E$488, E$489, E$490, E$491, E$492, E$493, E$494, E$495, E$496, E$497, E$498, E$499, E$500, E$501, E$502, E$503, E$504, E$505, E$506, E$507, E$508, E$509, E$510, E$511, E$512, E$513, E$514, E$553, E$554, E$555, E$556, E$557, E$558, E$559, E$560, E$561, E$562, E$563, E$564, E$565, E$566, E$567, E$568, E$569, E$570, E$571, E$572, E$573, E$574, E$575, E$576, E$577, E$578, E$579, E$580, E$581, E$582, E$583, E$584, E$585, E$586, E$587, E$588, E$589, E$590, E$591, E$592, E$593, E$594, E$595, E$596, E$597, E$598, E$599, E$600, E$601, E$602, E$603, E$604, E$605, E$606, E$607, E$608, E$609, E$610, E$611, E$612, E$613, E$614, E$615, E$616, E$617, E$618: 1X01
E$12, E$13, E$14, E$15, E$40, E$41, E$42, E$43, E$109, E$110, E$111, E$112, E$125, E$126, E$127, E$128, E$213, E$214, E$215, E$216, E$229, E$230, E$231, E$232, E$317, E$318, E$319, E$320, E$333, E$334, E$335, E$336, E$421, E$422, E$423, E$424, E$437, E$438, E$439, E$440, E$525, E$526, E$527, E$528, E$541, E$542, E$543, E$544: T-30_V
E$16, E$17, E$18, E$19, E$44, E$45, E$46, E$47, E$113, E$114, E$115, E$116, E$129, E$130, E$131, E$132, E$217, E$218, E$219, E$220, E$233, E$234, E$235, E$236, E$321, E$322, E$323, E$324, E$337, E$338, E$339, E$340, E$425, E$426, E$427, E$428, E$441, E$442, E$443, E$444, E$529, E$530, E$531, E$532, E$545, E$546, E$547, E$548: C2992
E$20, E$21, E$22, E$23, E$48, E$49, E$50, E$51, E$93, E$94, E$117, E$118, E$119, E$120, E$133, E$134, E$135, E$136, E$203, E$205, E$221, E$222, E$223, E$224, E$237, E$238, E$239, E$240, E$307, E$309, E$325, E$326, E$327, E$328, E$341, E$342, E$343, E$344, E$411, E$413, E$429, E$430, E$431, E$432, E$445, E$446, E$447, E$448, E$515, E$517, E$533, E$534, E$535, E$536, E$549, E$550, E$551, E$552, E$619, E$621: 0207/10
E$101, E$204, E$308, E$412, E$516, E$620: C5B2.5
E$103, E$207, E$311, E$415, E$519, E$623: 255SB
E$104, E$208, E$312, E$416, E$520, E$624: C5B7.2
E$105, E$206, E$310, E$414, E$518, E$622: ZDIO-10

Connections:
S$2: E$2.C, E$4.B, E$50.1
S$5: E$3.B, E$48.2
S$6: E$2.B, E$51.2
S$7: E$5.B, E$7.C, E$21.1
S$8: E$45.A, E$46.C
S$9: E$1.B, E$3.C, E$49.1
S$12: E$17.A, E$18.C
S$15: E$23.1, E$67.1
S$16: E$6.C, E$8.B, E$22.1
S$17: E$6.B, E$23.2
S$18: E$51.1, E$64.1
S$19: E$16.A, E$19.C
S$21: E$7.B, E$20.2
S$22: E$44.A, E$47.C
S$23: E$48.1, E$65.1
S$25: E$1.C, E$4.C, E$29.1, E$44.C, E$45.C, E$49.2, E$50.2, E$58.1, E$59.1, E$101.2, E$103.3, E$104.2
S$28: E$5.C, E$8.C, E$16.C, E$17.C, E$21.2, E$22.2, E$70.1, E$105.C
S$29: E$2.E, E$3.E, E$6.E, E$7.E, E$18.A, E$19.A, E$46.A, E$47.A, E$71.1, E$97.1, E$101.1, E$104.1
S$33: E$102.B, E$107.C, E$118.1
S$36: E$20.1, E$66.1
S$37: E$106.C, E$108.B, E$119.1
S$40: E$121.B, E$123.C, E$134.1
S$43: E$122.C, E$124.B, E$135.1
S$44: E$130.A, E$131.C
S$45: E$129.A, E$132.C
S$46: E$133.1, E$168.1
S$47: E$120.1, E$166.1
S$48: E$117.1, E$167.1
S$51: E$114.A, E$115.C
S$52: E$113.A, E$116.C
S$53: E$121.C, E$124.C, E$129.C, E$130.C, E$134.2, E$135.2, E$172.1, E$206.C
S$54: E$136.1, E$169.1
S$55: E$107.B, E$117.2
S$56: E$106.B, E$120.2
S$57: E$122.B, E$136.2
S$58: E$123.B, E$133.2
S$59: E$106.E, E$107.E, E$115.A, E$116.A, E$122.E, E$123.E, E$131.A, E$132.A, E$173.1, E$199.1, E$204.1, E$208.1
S$61: E$102.C, E$108.C, E$113.C, E$114.C, E$118.2, E$119.2, E$142.1, E$157.1, E$158.1, E$204.2, E$207.3, E$208.2
S$65: E$209.B, E$211.C, E$222.1
S$68: E$210.C, E$212.B, E$223.1
S$71: E$225.B, E$227.C, E$238.1
S$74: E$226.C, E$228.B, E$239.1
S$75: E$234.A, E$235.C
S$76: E$233.A, E$236.C
S$77: E$237.1, E$272.1
S$78: E$224.1, E$270.1
S$79: E$221.1, E$271.1
S$82: E$218.A, E$219.C
S$83: E$217.A, E$220.C
S$84: E$225.C, E$228.C, E$233.C, E$234.C, E$238.2, E$239.2, E$276.1, E$310.C
S$85: E$240.1, E$273.1
S$86: E$211.B, E$221.2
S$87: E$210.B, E$224.2
S$88: E$226.B, E$240.2
S$89: E$227.B, E$237.2
S$90: E$210.E, E$211.E, E$219.A, E$220.A, E$226.E, E$227.E, E$235.A, E$236.A, E$277.1, E$303.1, E$308.1, E$312.1
S$92: E$209.C, E$212.C, E$217.C, E$218.C, E$222.2, E$223.2, E$246.1, E$261.1, E$262.1, E$308.2, E$311.3, E$312.2
S$96: E$313.B, E$315.C, E$326.1
S$99: E$314.C, E$316.B, E$327.1
S$102: E$329.B, E$331.C, E$342.1
S$105: E$330.C, E$332.B, E$343.1
S$106: E$338.A, E$339.C
S$107: E$337.A, E$340.C
S$108: E$341.1, E$376.1
S$109: E$328.1, E$374.1
S$110: E$325.1, E$375.1
S$113: E$322.A, E$323.C
S$114: E$321.A, E$324.C
S$115: E$329.C, E$332.C, E$337.C, E$338.C, E$342.2, E$343.2, E$380.1, E$414.C
S$116: E$344.1, E$377.1
S$117: E$315.B, E$325.2
S$118: E$314.B, E$328.2
S$119: E$330.B, E$344.2
S$120: E$331.B, E$341.2
S$121: E$314.E, E$315.E, E$323.A, E$324.A, E$330.E, E$331.E, E$339.A, E$340.A, E$381.1, E$407.1, E$412.1, E$416.1
S$123: E$313.C, E$316.C, E$321.C, E$322.C, E$326.2, E$327.2, E$350.1, E$365.1, E$366.1, E$412.2, E$415.3, E$416.2
S$127: E$417.B, E$419.C, E$430.1
S$130: E$418.C, E$420.B, E$431.1
S$133: E$433.B, E$435.C, E$446.1
S$136: E$434.C, E$436.B, E$447.1
S$137: E$442.A, E$443.C
S$138: E$441.A, E$444.C
S$139: E$445.1, E$480.1
S$140: E$432.1, E$478.1
S$141: E$429.1, E$479.1
S$144: E$426.A, E$427.C
S$145: E$425.A, E$428.C
S$146: E$433.C, E$436.C, E$441.C, E$442.C, E$446.2, E$447.2, E$484.1, E$518.C
S$147: E$448.1, E$481.1
S$148: E$419.B, E$429.2
S$149: E$418.B, E$432.2
S$150: E$434.B, E$448.2
S$151: E$435.B, E$445.2
S$152: E$418.E, E$419.E, E$427.A, E$428.A, E$434.E, E$435.E, E$443.A, E$444.A, E$485.1, E$511.1, E$516.1, E$520.1
S$154: E$417.C, E$420.C, E$425.C, E$426.C, E$430.2, E$431.2, E$454.1, E$469.1, E$470.1, E$516.2, E$519.3, E$520.2
S$158: E$521.B, E$523.C, E$534.1
S$161: E$522.C, E$524.B, E$535.1
S$164: E$537.B, E$539.C, E$550.1
S$167: E$538.C, E$540.B, E$551.1
S$168: E$546.A, E$547.C
S$169: E$545.A, E$548.C
S$170: E$549.1, E$584.1
S$171: E$536.1, E$582.1
S$172: E$533.1, E$583.1
S$175: E$530.A, E$531.C
S$176: E$529.A, E$532.C
S$177: E$537.C, E$540.C, E$545.C, E$546.C, E$550.2, E$551.2, E$588.1, E$622.C
S$178: E$552.1, E$585.1
S$179: E$523.B, E$533.2
S$180: E$522.B, E$536.2
S$181: E$538.B, E$552.2
S$182: E$539.B, E$549.2
S$183: E$522.E, E$523.E, E$531.A, E$532.A, E$538.E, E$539.E, E$547.A, E$548.A, E$589.1, E$615.1, E$620.1, E$624.1
S$185: E$521.C, E$524.C, E$529.C, E$530.C, E$534.2, E$535.2, E$558.1, E$573.1, E$574.1, E$620.2, E$623.3, E$624.2

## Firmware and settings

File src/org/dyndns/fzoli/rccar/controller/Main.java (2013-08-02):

package org.dyndns.fzoli.rccar.controller;

import chrriis.dj.nativeswing.swtimpl.NativeInterfaceAdapter;
import org.dyndns.fzoli.rccar.SplashScreenLoader;
import java.awt.GraphicsEnvironment;
import java.awt.Toolkit;
import java.awt.event.ActionEvent;
import java.awt.event.ActionListener;
import java.awt.event.WindowAdapter;
import java.awt.event.WindowEvent;
import java.awt.image.BufferedImage;
import java.io.IOException;
import java.util.Locale;
import java.util.ResourceBundle;
import java.util.Timer;
import java.util.TimerTask;
import javax.swing.SwingUtilities;
import static org.dyndns.fzoli.rccar.SplashScreenLoader.setSplashMessage;
import org.dyndns.fzoli.rccar.controller.resource.R;
import org.dyndns.fzoli.rccar.controller.socket.ConnectionHelper;
import org.dyndns.fzoli.rccar.controller.view.ConnectionProgressFrame;
import org.dyndns.fzoli.rccar.controller.view.ConnectionProgressFrame.Status;
import org.dyndns.fzoli.rccar.controller.view.config.ConfigEditorFrame;
import org.dyndns.fzoli.rccar.model.controller.HostList;
import org.dyndns.fzoli.rccar.ui.UIUtil;
import org.dyndns.fzoli.rccar.ui.UncaughtExceptionHandler;
import org.dyndns.fzoli.ui.LanguageChooserFrame;
import org.dyndns.fzoli.ui.OptionPane;
import org.dyndns.fzoli.ui.OptionPane.PasswordData;
import static org.dyndns.fzoli.rccar.ui.UIUtil.setSystemLookAndFeel;
import static org.dyndns.fzoli.rccar.ui.UIUtil.initNativeInterface;
import static org.dyndns.fzoli.rccar.ui.UIUtil.addNativeInterfaceListener;
import static org.dyndns.fzoli.rccar.ui.UIUtil.runNativeEventPump;
import org.dyndns.fzoli.ui.systemtray.SystemTrayIcon;
import static org.dyndns.fzoli.ui.systemtray.SystemTrayIcon.showMessage;
import org.dyndns.fzoli.ui.systemtray.TrayIcon.IconType;
import static org.dyndns.fzoli.util.OSUtils.setApplicationName;
import org.dyndns.fzoli.ui.systemtray.MenuItem;
import org.dyndns.fzoli.ui.systemtray.MenuItemReference;
import static org.dyndns.fzoli.util.MacApplication.setDockIcon;
import org.dyndns.fzoli.util.OSUtils;

/**
 * A vezérlő indító osztálya.
 * @author zoli
 */
public class Main {
    
    /**
     * Új sor jel.
     */
    public static final String LS = System.getProperty("line.separator");
    
    /**
     * Callback, ami megjeleníti a kapcsolatbeállító ablakot.
     */
    private static final Runnable CALLBACK_SETTING = new Runnable() {

        @Override
        public void run() {
            // kapcsolatbeállító ablak megjelenítése
            showSettingFrame(false, null);
        }

    };
    
    /**
     * Callback, ami akkor fut le, ha ki szeretnének lépni a programból.
     */
    private static final Runnable CALLBACK_EXIT = new Runnable() {
        
        /**
         * Ha a kilépésre kattintottak.
         * A program azonnal végetér, ha nincs kiépítve kapcsolat,
         * egyébként megkérdezi a felhasználót, hogy biztos ki akar-e lépni
         * és csak akkor lép ki, ha Igen a válasza.
         * Mac-en nem teszi fel a kérdést, egyből kilép, mivel a dialógusablakok
         * nem mindig kerülnek előtérbe és zavaróak.
         */
        @Override
        public void run() {
            if (CONN.isConnected() && !OSUtils.isOS(OSUtils.OS.MAC)) { // ha van kiépített kapcsolat
                // megkérdi, biztos-e a kilépésben
                int opt = OptionPane.showYesNoDialog(SELECTION_FRAME, getString("confirm_exit"), getString("confirmation"));
                // ha igen, akkor a program kilép
                if (opt == 0) {
                    exit();
                }
            }
            else { // ha nincs kiépített kapcsolat, a program kilép
                exit();
            }
        }

    };
    
    /**
     * Eseményfigyelő, ami akkor fut le, ha ki szeretnének lépni a programból.
     */
    private static final ActionListener AL_EXIT = new ActionListener() {
        
        @Override
        public void actionPerformed(ActionEvent e) {
            CALLBACK_EXIT.run();
        }

    };
    
    /**
     * A konfiguráció beállító ablak bezárásakor figyelmeztetést jelentít meg, ha kell.
     */
    private static final WindowAdapter WL_CFG = new WindowAdapter() {

        @Override
        public void windowClosed(WindowEvent e) {
            configAlert(false);
        }

    };
    
    /**
     * A Natív Interfész bezárásakor lefutó eseményfigyelő, ami a rendszerikont újrainicializálja AWT alapokon.
     */
    private static final NativeInterfaceAdapter NI_LISTENER = new NativeInterfaceAdapter() {

        private boolean closed = false;
        
        @Override
        public void nativeInterfaceClosed() {
            if (closed) return;
            closed = true;
            setSystemTrayIcon();
        }
        
    };
    
    /**
     * A konfigurációt tartalmazó objektum.
     */
    private static final Config CONFIG = Config.getInstance();
    
    /**
     * A szótár.
     */
    private static ResourceBundle STRINGS = createResource(CONFIG.getLanguage());
    
    /**
     * A Híd szerverrel építi ki a kapcsolatot.
     */
    private static final ConnectionHelper CONN = new ConnectionHelper(CONFIG);
    
    /**
     * Időzítő a Híd szerverhez való kapcsolódás késleltetéséhez.
     */
    private static final Timer TIMER_CONN = new Timer();
    
    /**
     * Ha az értéke true, akkor a program leállítás alatt van.
     * Ez esetben a kapcsolódáskezelő ablak nem jelenik meg, amikor megszakad a híddal a kapcsolat.
     */
    private static boolean exiting = false;
    
    /**
     * Nyelvkiválasztó ablak.
     */
    public static LanguageChooserFrame LNG_FRAME;
    
    /**
     * Konfiguráció-szerkesztő ablak.
     */
    private static ConfigEditorFrame CONFIG_EDITOR;
    
    /**
     * Kapcsolódásjelző- és kezelő ablak.
     */
    private static ConnectionProgressFrame PROGRESS_FRAME;
    
    /**
     * Járműválasztó ablak.
     */
    private static HostSelectionFrame SELECTION_FRAME;
    
    /**
     * A kiválasztott járműhöz tartozó ablakok konténere.
     */
    private static ControllerWindows CONTROLLER_WINDOWS;
    
    /**
     * A szerző dialógust megjelenítő menüelem, ami inaktív,
     * míg a dialógus látható.
     */
    private static MenuItem MI_ABOUT;
    
    /**
     * Újrakapcsolódás menüopció.
     */
    private static MenuItem MI_RECONNECT;
    
    /**
     * Segédváltozó kapcsolódás kérés detektálására.
     */
    private static boolean connecting = false;
    
    /**
     * A program leállítása.
     * Akkor fut le, amikor a felhasználó ki szeretne lépni a programból.
     */
    private static void exit() {
        exiting = true;
        SystemTrayIcon.dispose();
        UncaughtExceptionHandler.setDisabled(true);
        System.exit(0);
    }
    
    /**
     * Beállítja a híd kivételkezelő metódusát.
     * Ha a rendszerikonok támogatva vannak, dialógusablak jeleníti meg a nem kezelt kivételeket,
     * egyébként nem változik az eredeti kivételkezelés.
     */
    private static void setExceptionHandler() {
        UncaughtExceptionHandler.apply(R.getIconImage());
    }
    
    /**
     * Beállítja a rendszerikont.
     */
    private static void setSystemTrayIcon() {
        if (SystemTrayIcon.init(!UIUtil.isNativeSwingAvailable()) && SystemTrayIcon.isSupported()) {
            // az ikon beállítása
            SystemTrayIcon.setIcon(getString("app_name"), R.resize(R.getIconImage(), SystemTrayIcon.getIconWidth()));
            // nyelv választó opció hozzáadása
            String lngText = getString("language");
            if (!lngText.equalsIgnoreCase("language")) lngText += " (language)";
            SystemTrayIcon.addMenuItem(lngText, R.getImage("languages.png"), new Runnable() {

                @Override
                public void run() {
                    if (LNG_FRAME != null) LNG_FRAME.setVisible(true);
                }

            });

            //szeparátor hozzáadása
            SystemTrayIcon.addMenuSeparator();

            // kapcsolatbeállítás opció hozzáadása
            SystemTrayIcon.addMenuItem(getString("connection_settings"), R.getImage("preferences.png"), CALLBACK_SETTING);

            // újrakapcsolódás opció hozzáadása
            MI_RECONNECT = SystemTrayIcon.addMenuItem(getString("reconnect"), R.getImage("connect.png"), new Runnable() {

                @Override
                public void run() {
                    reconnect();
                }

            });

            //szeparátor hozzáadása
            SystemTrayIcon.addMenuSeparator();

            // megadja, hogy engedélyezett-e a névjegy megjelenítése
            boolean showAboutEnabled = true;
            if (MI_ABOUT != null) showAboutEnabled = MI_ABOUT.isEnabled();

            // az aktuális névjegy-megjelenítő opció referenciáját adja meg
            final MenuItemReference mirAuthor = new MenuItemReference() {

                @Override
                public synchronized MenuItem getMenuItem() {
                    return MI_ABOUT;
                }

            };

            // névjegy opció hozzáadása
            MI_ABOUT = SystemTrayIcon.addMenuItem(getString("about"), R.getQuestionImage(), new Runnable() {

                @Override
                public void run() {
                    UIUtil.showAuthorDialog(mirAuthor, R.getIconImage());
                }

            });

            // csak egyetlen névjegy ablak lehet látható egyazon időben
            MI_ABOUT.setEnabled(showAboutEnabled);
            
            // kilépés opció hozzáadása
            SystemTrayIcon.addMenuItem(getString("exit"), R.getExitImage(), CALLBACK_EXIT);
        }
    }
    
    /**
     * A beállításkezelő ablakot jeleníti meg.
     * Ha a helyes konfiguráció kényszerített, az ablak bezárása után figyelmeztetés jelenhet meg a beállításokkal kapcsolatban.
     * @param force kényszerítve legyen-e a felhasználó helyes konfiguráció megadására
     * @param tabIndex a megjelenő lapfül
     */
    public static void showSettingFrame(boolean force, Integer tabIndex) {
        if (!CONN.isConnected()) {
            CONN.disconnect();
        }
        if (PROGRESS_FRAME != null) {
            PROGRESS_FRAME.setVisible(false);
        }
        if (CONFIG_EDITOR != null) {
            if (SELECTION_FRAME != null && SELECTION_FRAME.isVisible()) {
                CONFIG_EDITOR.setLocationRelativeTo(SELECTION_FRAME);
            }
            CONFIG_EDITOR.setTabIndex(tabIndex);
            CONFIG_EDITOR.setForce(force);
            CONFIG_EDITOR.setVisible(true);
        }
    }
    
    /**
     * Hibaüzenetet küld a felhasználónak modális dialógusablakban.
     * @param text a megjelenő szöveg
     */
    private static void showSettingError(String text) {
        UIUtil.alert(getString("error"), text, System.err, R.getIconImage());
    }
    
    /**
     * Figyelmeztetést küld a felhasználónak a buborékablakra.
     * Az üzenetre kattintva a kapcsolatbeállító ablak jelenik meg.
     * @param text a megjelenő szöveg
     * @param showSettings jelenjen-e meg a beállítások ablak kattintás esetén
     */
    private static void showSettingWarning(String text, boolean showSettings) {
        showMessage(getString("warning"), text, IconType.WARNING, showSettings ? CALLBACK_SETTING : null);
    }
    
    /**
     * Közli a felhasználóval, hogy a kapcsolódás folyamatban van.
     * Ha a nyitóképernyő még látható, akkor azon történik a jelzés, egyébként
     * a kapcsolódásjelző ablak jelenik meg.
     */
    private static void showConnecting() {
        if (SplashScreenLoader.isVisible()) {
            SplashScreenLoader.setSplashMessage(getString("connect_to_server"));
        }
        else {
            showConnectionStatus(Status.CONNECTING);
        }
    }
    
    /**
     * Beállítja a kapcsolatjelző ablakon a látható ikont és szöveget, majd elrejti a többi ablakot.
     * Ha nincs megadva státusz, akkor az ablak eltűnik, egyébként a megadott státusz jelenik meg.
     * Ha éppen kapcsolódás van, csak a kapcsolódás státusz állítható be.
     * Ha a kapcsolatbeállító ablak látható vagy a program leállítás alatt van,
     * nem jelenik meg a kapcsolatjelző ablak.
     * @param status a kapcsolat státusza
     */
    public static void showConnectionStatus(Status status) {
        if (exiting || CONFIG_EDITOR.isVisible()) return;
        if (connecting && status != Status.CONNECTING) return;
        PROGRESS_FRAME.setStatus(status, MI_RECONNECT);
        SELECTION_FRAME.setVisible(false);
        CONTROLLER_WINDOWS.setVisible(false);
    }
    
    /**
     * Megjeleníti a járműválasztó ablakot és elrejti a járművel kapcsolatos ablakokat.
     * @param l a teljes lista, ami az összes jármű nevét tartalmazza
     */
    public static void showHostSelectionFrame(HostList l) {
        SELECTION_FRAME.refresh(l.getHosts());
        if (!SELECTION_FRAME.isVisible()) {
            SELECTION_FRAME.setVisible(true);
            CONTROLLER_WINDOWS.setVisible(false);
        }
    }
    
    /**
     * A kiválasztott járműhöz tartozó ablakokat jeleníti meg és elrejti a járműválasztót.
     */
    public static void showControllerWindows() {
        CONTROLLER_WINDOWS.setVisible(true);
        SELECTION_FRAME.setVisible(false);
    }
    
    /**
     * Megjeleníti a jelszóbekérő dialógust és ha megadták, elmenti a jelszót a memóriába vagy a konfig fájlba.
     * Ha a kapcsolódásjelző ablak nem látható, akkor a jelszókérő dialógus megjelenik a tálcán.
     * @return a megadott jelszó adat, ami akkor null, ha a Beállítások gombra kattintottak
     */
    public static PasswordData showPasswordDialog() {
        PasswordData data = UIUtil.showPasswordInput(R.getIconImage(), true, !PROGRESS_FRAME.isVisible(), getString("settings"), new Runnable() {

            @Override
            public void run() {
                showSettingFrame(false, 1);
            }

        });
        if (data != null) {
            CONFIG.setPassword(data.getPassword(), data.isSave());
            if (data.isSave()) Config.save(CONFIG);
        }
        return data;
    }
    
    /**
     * Frissíti az MJPEG képkockát a felületen.
     * @param frame a képkocka, ami ha null, fekete kitöltésű kép jelenik meg
     */
    public static void setMjpegFrame(BufferedImage frame) {
        CONTROLLER_WINDOWS.setMjpegFrame(frame);
    }
    
    /**
     * Ha van kiépítve kapcsolat, bontja azt és új kapcsolatot alakít ki.
     */
    public static void reconnect() {
        if (CONN.isConnecting()) return;
        CONN.disconnect();
        runClient(true, false);
    }
    
    /**
     * A program értelme.
     * Kijelzi, hogy elkezdődött a kapcsolódás és kapcsolódik a szerverhez (ha még nem történt meg).
     * Innentől kezdve már a kommunikációtól függ, hogyan folytatódik a program futása.
     * @param reloadMap legyen-e újratöltve a térkép dialóus
     */
    public static void runClient(boolean reloadMap) {
        runClient(false, reloadMap);
    }
    
    /**
     * A program értelme.
     * Kijelzi, hogy elkezdődött a kapcsolódás és kapcsolódik a szerverhez (ha még nem történt meg).
     * Fél másodperc késleltetés van beállítva, hogy legyen ideje a felhasználónak észlelni a folyamatot,
     * és így a szervernek is van ideje bezárni a régi kapcsolatokat és frissíteni az adatokat.
     * Innentől kezdve már a kommunikációtól függ, hogyan folytatódik a program futása.
     * @param delay legyen-e késleltetés
     * @param reloadMap legyen-e újratöltve a térkép dialóus
     */
    public static void runClient(boolean delay, final boolean reloadMap) {
        if (connecting || CONN.isConnected()) return;
        connecting = true;
        showConnecting();
        TIMER_CONN.schedule(new TimerTask() {
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
    public static void main(String[] args) {
        setApplicationName("Mobile-RC"); // alkalmazásnév beállítása
        setSplashMessage(getString("please_wait")); // jelzés a felhasználónak, hogy tölt a program
        initNativeInterface(); // natív interfész inicializálása a webböngészőhöz és a rendszerikonhoz
        addNativeInterfaceListener(NI_LISTENER); // natív interfész eseménykezelő hozzáadása
        setSystemLookAndFeel(); // rendszer LAF beállítása
        setDockIcon(R.getIconImage()); // Mac OS X-en dock ikon beállítása az alkalmazásválasztó ikonjára
        setExceptionHandler(); // kivételkezelő átállítása a kivételt megjelenítő dialógusra
        if (GraphicsEnvironment.isHeadless()) { // ha a grafikus felület nem érhető el
            System.err.println(getString("msg_need_gui") + LS + getString("msg_exit"));
            System.exit(1); // hibakóddal lép ki
        }
        SwingUtilities.invokeLater(new Runnable() {

            @Override
            public void run() {
                setSystemTrayIcon(); // rendszerikon létrehozása
                
                if (!Config.STORE_FILE.exists()) { // ha a konfig fájl nem létezik
                    try {
                        if (!Config.ROOT.exists()) Config.ROOT.mkdirs(); // könyvtár létrehozása, ha nem létezik még
                        Config.STORE_FILE.createNewFile(); // megpróbálja létrehozni
                        Config.STORE_FILE.delete(); // és törli, ha sikerült a létrehozás
                    }
                    catch (IOException ex) { // ha nem lehet létrehozni a fájlt: jogosultság gond
                        showSettingError(getString("msg_need_dir_permission") + LS + getString("msg_dir_path") + ": " + Config.ROOT.getAbsolutePath() + LS + getString("msg_exit"));
                        System.exit(1);
                    }
                }
                if (Config.STORE_FILE.exists() && (!Config.STORE_FILE.canRead() || !Config.STORE_FILE.canWrite())) {
                    showSettingError(getString("msg_need_cfg_permission") + LS + getString("msg_file_path") + ": " + Config.STORE_FILE.getAbsolutePath() + LS + getString("msg_exit"));
                    System.exit(1);
                }
                
                // Előinicializálom az ablakokat, míg a nyitóképernyő fent van,
                // hogy később ne menjen el ezzel a hasznos idő.
                // A nyelvkiválasztó ablakkal kezdem, mivel a konfig-szerkesztő
                // ablak használja a referenciáját.
                
                LNG_FRAME = new LanguageChooserFrame(R.getIconImage(), "org.dyndns.fzoli.rccar.l10n", "controller", CONFIG.getLanguage(), Locale.ENGLISH, new Locale("hu")) {

                    /**
                     * Ha a nyelv megváltozott, kért nyelv beállítása.
                     */
                    @Override
                    protected void onLanguageSelected(Locale l) {
                        Main.setLanguage(l);
                    }
                    
                };
                PROGRESS_FRAME = new ConnectionProgressFrame(CALLBACK_EXIT);
                CONFIG_EDITOR = new ConfigEditorFrame(CONFIG, WL_CFG);
                if (OSUtils.isOS(OSUtils.OS.MAC) && CONFIG.needInfo()) {
                    // Mac alatt az ablakok előtérbe kerülése nem mindig sikerül
                    // Figyelmeztetem a felhasználót, hogy a modális dialógusok blokkolják a felületet
                    // és ha úgy tűnik, nem válaszol a program, az ablakok elmozdításával egy háttérbe
                    // került modális dialógusablakot találhatnak. A pozícionálási hiba oka ismeretlen...
                    OptionPane.showMessageDialog(R.getIconImage(),
                            getString("warn_testing1") + LS + LS +
                            getString("warn_testing2") + LS + getString("warn_testing3") + LS +
                            getString("warn_testing4") + LS + LS +
                            getString("warn_testing5"), getString("warn_testing1"),
                            OptionPane.INFORMATION_MESSAGE, true);
                }
                if (!CONFIG.isCorrect()) { // ha a tanúsítvány fájlok egyike nem létezik
                    showSettingError(getString("warn_config_error1" + (CONFIG.isDefault() ? 'b' : 'a')) + ' ' + getString("warn_config_error2") + LS + getString("warn_config_error3"));
                    showSettingFrame(true, 1); // kényszerített beállítás és tanúsítvány lapfül előtérbe hozása
                }
                SELECTION_FRAME = new HostSelectionFrame(AL_EXIT);
                CONTROLLER_WINDOWS = new ControllerWindows();
                Toolkit.getDefaultToolkit().sync(); // addig nem indul a kliens, míg a felület készen nem áll
                if (CONFIG.isCorrect()) { // ha a konfiguráció megfelelő, kliens indítása
                    configAlert(true); // súgó figyelmeztetés, ha kell
                    runClient(false); // és végül a lényeg
                }
            }

        });
        runNativeEventPump(); // natív interfész eseménypumpáló indítása
    }
    
}

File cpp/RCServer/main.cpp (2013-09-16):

/* 
 * File:   main.cpp
 * Author: zoli
 * 
 * Created on 2013. szeptember 1., 19:59
 */

#include <iostream>
#include <unistd.h>
#include <signal.h>
#include <stdlib.h>
#include <stdio.h>

#include "SSLServerSocket.h"
#include "CertificateException.h"
#include "Config.h"
#include "BridgeHandler.h"

SSLServerSocket *s = NULL;

void exitHandler(int signal) {
    if (s != NULL) s->close();
}

void createServerSocket(Config *c) {
    std::string CAfile = c->getCaFile();
    std::string CRTfile = c->getCertFile();
    std::string KEYfile = c->getKeyFile();
    char *KEYpass = (char *) c->getPassword().c_str();
    s = new SSLServerSocket(c->getPort(), CAfile.c_str(), CRTfile.c_str(), KEYfile.c_str(), KEYpass);
    s->setTimeout(3);
    
    struct sigaction sigHandler;
    sigHandler.sa_handler = exitHandler;
    sigHandler.sa_flags = 0;
    sigemptyset(&sigHandler.sa_mask);
    sigaction(SIGINT, &sigHandler, NULL);
    sigaction(SIGTERM, &sigHandler, NULL);
    
    struct sigaction sigPipeHandler;
    sigPipeHandler.sa_handler = SIG_IGN;
    sigPipeHandler.sa_flags = 0;
    sigemptyset(&sigPipeHandler.sa_mask);
    sigaction(SIGPIPE, &sigPipeHandler, NULL);
}

int main(int argc, char** argv) {
    Config c("bridge.conf");
    if (!c.isCorrect()) {
        std::cerr << "Incorrect config file.\n";
        return EXIT_FAILURE;
    }
    try {
        createServerSocket(&c);
        while (!s->isClosed()) {
            try {
                new BridgeHandler(s->accept());
            }
            catch (SocketException &ex) {
                if (s->isClosed()) return EXIT_SUCCESS;
                std::cerr << "Connection error: " + ex.msg() + "\n";
            }
        }
    }
    catch (SocketException &ex) {
        std::cerr << "Server could not be created.\n";
        return EXIT_FAILURE;
    }
    return EXIT_SUCCESS;
}

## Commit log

2012-10-30 ArrayList switched to thread safe List
2012-10-31 IOIO lib added
    [proguard.cfg]
2012-11-06 TODO: bug - disconnect not detected
    [Main.java]
2012-11-06 incompatible class handling added
    [Main.java]
2012-11-14 swt tray freeze bug resolved
    [Main.java]
2012-12-07 pcb design
    [pcb.brd]
2012-12-11 pcb pdf added
    [pcb_v3.brd]
2012-12-11 pcb test pdf added
2012-12-21 pcb test update
    [testC.brd]
2012-12-31 MapDialog thread fix
2013-01-02 pcb update
    [testK.brd, tmp.brd]
2013-01-02 thread bugfix
2013-01-08 controller frame border changed
2013-01-10 password reset button added
2013-01-18 android update: PWM controll and voltage display added
2013-01-26 jipCam is rebuilt without exception printing
2013-02-21 language files are replaced
    [Main.java]
2013-03-26 setting button is added
2013-04-05 changeable voltage thresholds
2013-04-05 pcb uploading
    [pcb_v4.brd, testA.brd, testB.brd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]
2013-04-06 min/max voltage threshold options are added
2013-04-22 position of about frame is changed
2013-04-23 release v1.0.0.2 error dialogs display the file path
    [Main.java]
2013-04-25 release v1.0.3.7 magnetic declination is added to the Android code
2013-04-25 release v1.0.3.8 sensor timeout is increased
2013-05-08 system tray test frame is created
2013-05-20 BJT H Bridge picture has been saved
    [base.sch]
2013-05-22 BJT H Bridge picture has been edited
    [base.sch]
2013-05-26 PCB note has been edited
    [base_pcb.ods, pcb_v4.brd]
2013-06-01 default pcb photo
2013-07-26 release v1.1.12.21 mjpeg streaming won't stop
    [Main.java]
2013-08-27 android release v1.2.2.31 PWM40 test
2013-08-30 android release v1.3.0.35 IOIO Bluetooth Lib has been added
    [proguard.cfg]
2013-08-30 PWM40 test
2013-09-08 DeviceHandler class
